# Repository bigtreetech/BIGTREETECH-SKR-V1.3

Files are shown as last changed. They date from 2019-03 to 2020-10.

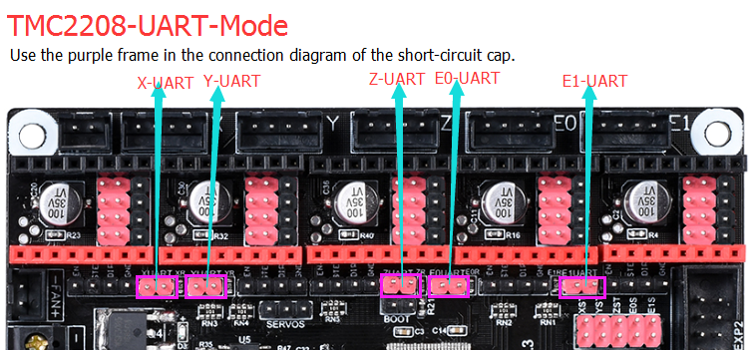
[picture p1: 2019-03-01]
BTT SKR V1.3/Wiring diagram/SKR V1.3-TMC2208-UART-Mode.png

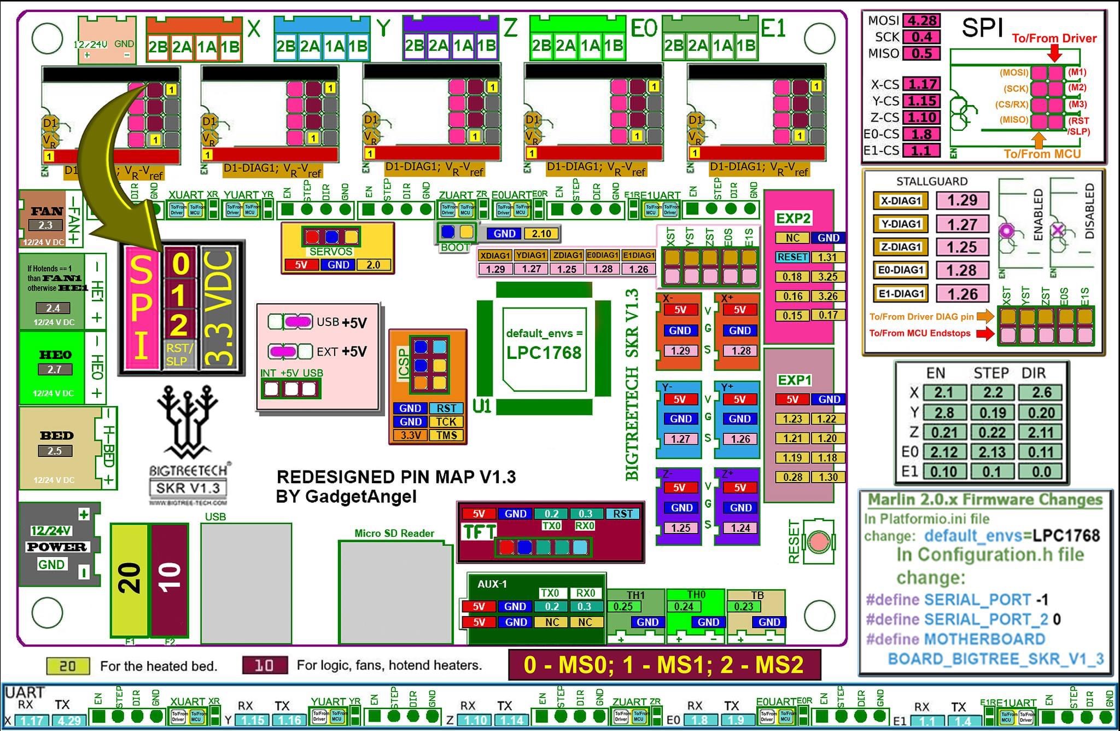
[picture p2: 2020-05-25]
BTT SKR V1.3/hardware/SKR-V1.3-pinout.jpg

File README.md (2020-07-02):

# BIGTREETECH-SKR-V1.3
32bit board with LPC1768, support marlin2.0 and smoothieware, support lcd2004/12864, On-board TMC2130 SPI interface and TMC2208 UART interface no additional wiring is 

BIGTREETECH SKR V1.3 YouTube Video：[here](https://www.youtube.com/watch?v=oaXfXkPYHpw&t=8s)
 
# BIGTREETECH-SKR-V1.4
This [article](https://3dwork.io/en/complete-guide-skr-v1-4-and-tmc2209) explains how to configure all different TMC2209 dirvers from different procuders in SKR V1.4 & V1.4 Turbo

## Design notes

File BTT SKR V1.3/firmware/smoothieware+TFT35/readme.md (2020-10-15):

If you are using smootheware firmware, please disable the LEDs event in the configuration file,  as shown below
> leds_disable                        true

> play_led_disable                    true



Because there is no led on SKR V1.3, and the IO used by the LED on smoothieboard is of other use in SKR V1.3. If the LED is not disabled, other functions may be abnormal

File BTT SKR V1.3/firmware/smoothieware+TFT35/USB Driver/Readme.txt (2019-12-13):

USB Driver Installation tutorial £º
                                   http://smoothieware.org/windows-drivers

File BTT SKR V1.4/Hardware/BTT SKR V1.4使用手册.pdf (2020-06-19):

### 深圳市必趣科技有限公司 BIG TREE TECH

# BIGTREETECH SKR V1.4

# 主板使用说明书

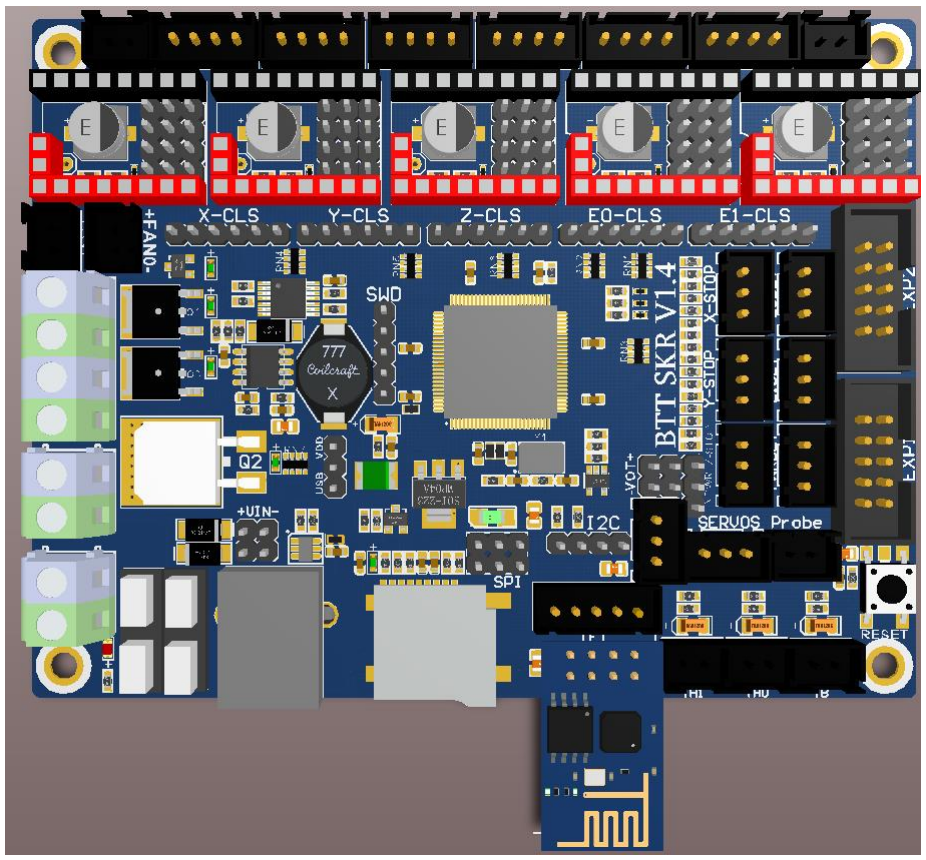
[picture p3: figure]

### BIG TREE TECH

# 一、SKR 主板简介

BIGTREETECH SKR V1.4 主板是深圳必趣科技有限公司 3D 打印

### 团队针对V1.3版本存在的不足进行优化升级的32位3D打印机主板，

### 特别适合中小型打印机使用。

## 1. SKR 主板特点：

1）采用 32 位主频 100MHz 的 ARM 级 Cortex-M3 系列 LPC1768 主控芯片， 性能大幅提升；
2）搭载高度模块化开源固件 Marlin2.0，方便用户 DIY 及二次开发； 3）采用专用电源芯片 M6130，支持 12-24V 电源输入；
4）支持 2.4、2.8、3.5 寸彩色触摸屏，支持 LCD2004 屏、LCD12864 屏； 5）通过 SD 卡升级配置固件，操作简单方便高效；
6）板载 TMC 驱动的 SPI 工作模式和 UART 工作模式，且板载 DIAG 功能引 脚，方便客户使用，省去复杂的接线过程，只需通过简单的拔插跳线帽即可使用； 7）支持断电续打、断料检测、打完关机等功能；
8）采用高性能 MOSFET 管，散热效果更好；
9）采用可拔插的保险丝，是更换过程更加简易；
10）预留 BLTouch 接口 SERVOS 和 Probe，方便使用 BL Touch；
11）支持 RGB 灯条；
12）使用电源选择设计，让 USB 电源与开关电源分开，有效避免由于短路 导致电脑 USB 口被烧毁的情况发生；
13）特殊功能接口使用颜色显眼的排针，大大减少接线的错误率。 14）预留 I2C、SPI、WIFI 接口，方便客户 DIY； 15）预留闭环驱动接口，省去外插转接模块的烦恼；
16）双 Z 轴接口，省去外接驱动拓展模块的烦恼；
17）热敏电阻接口使用胆电容加压敏电阻进行保护，增强接口的抵抗能力； 18）更多的风扇接口：1 路数控风扇，3 路常开风扇；
19）可插外接 DC5V 电源模块，给 TFT 屏、BLtouch、Neopixel 供电。

## 2. SKR 主板参数：

外观尺寸：110*85mm
安装尺寸：102*76mm
微处理器：ARM Cortex-M3 CPU
输入电压：DC12V-DC24V 5A-15A
逻辑电压：DC 3.3V
WIFI 模块：ESP-01S
电机驱动器：支持 TMC5161、TMC5160、TMC2209、TMC2225、TMC2208、 TMC2130、ST820、LV8729、DRV8825、A4988 等，可单独外接电机驱动 驱动工作模式支持：SPI、UART、STEP/DIR

### BIG TREE TECH

电机驱动接口：X、Y、Z、E0、E1，五路（各路都有一个闭环驱动接口）， 最高可达 256 细分
温度传感器接口：TH0、TH1、TB，3 路 100K NTC（热电阻） 显示屏：2.4、2.8、3.5 寸 TFT（支持双模式屏）、LCD2004、LCD12864 PC 通信接口：方形 USB，方便插拔，通信波特率 115200 拓展接口功能支持：断料检测，断电续打，打完关机，自动调平，BL Touch 支持文件格式：G-code
支持机器结构：XYZ、delta、kossel、Ultimaker、corexy 推荐软件：Cura、Simplify3D、pronterface、Repetier-host、Makerware

# 二、SKR 主板通电

SKR 主板上电之后，左下角的 D5 红灯会亮起，表示供电正常；板子中部的 5V SEL 是电源选择端；
1）当使用 USB 给主板供电时：

2）当使用 12V-24V 供电时：

# 三、SKR 主板与电脑通信

SKR 主板通过【USB】接口与电脑通信，需要电脑先安装驱动程序后，再将 主板插入电脑，方可识别端口进行数据传输。不安装驱动程序就容易出现电脑无 法识别 USB 端口的现象，
使用 Marlin2.0 固件，则是参照教程进行安装：

教程：https://www.dropbox.com/s/ppjfflhf3j5yzh2/MarlinV2.0%20SKRV1.1%20instruction.docx?dl=0驱动：https://www.dropbox.com/s/a0k5idjmf4fn82f/lpc176x_usb_driver.inf?dl=0

# 四、SKR 主板接口说明

1. SKR 主板尺寸图

### BIG TREE TECH

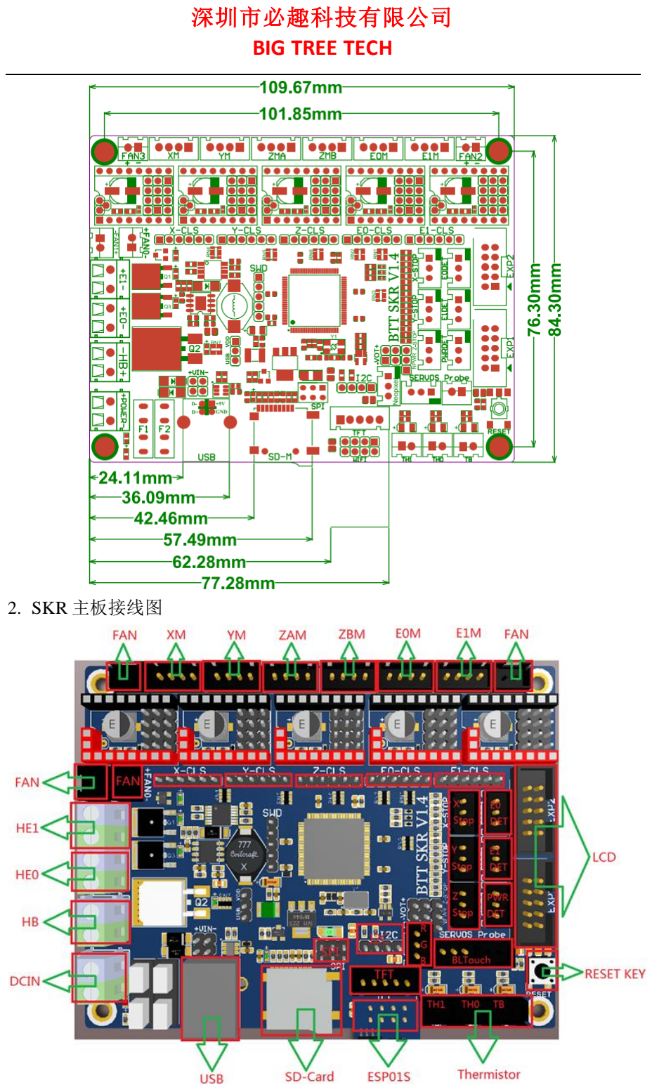
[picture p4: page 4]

2. SKR 主板接线图

### BIG TREE TECH

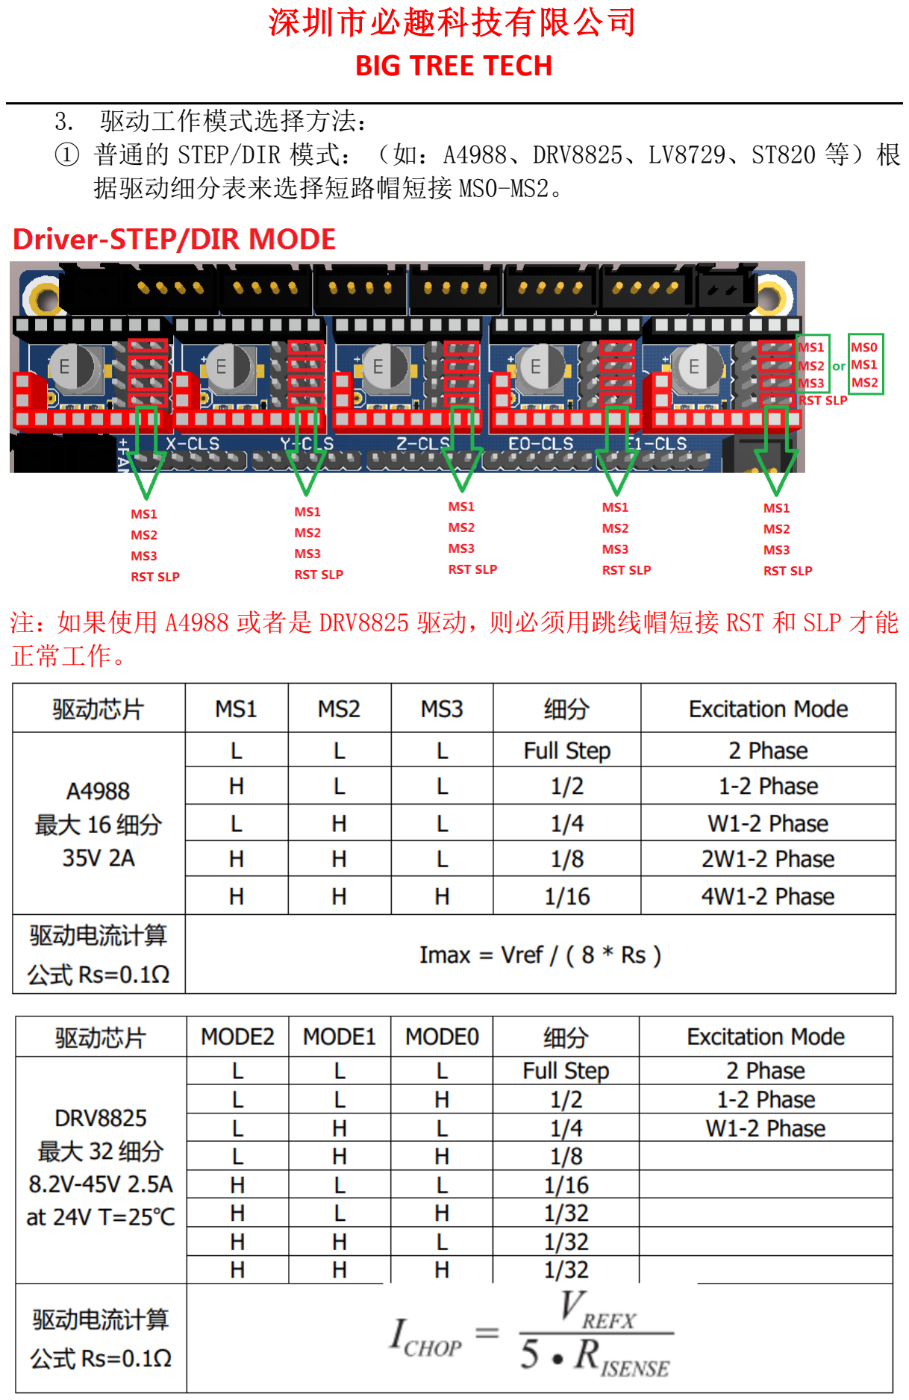
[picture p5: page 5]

3. 驱动工作模式选择方法：
① 普通的 STEP/DIR 模式：（如：A4988、DRV8825、LV8729、ST820 等）根 据驱动细分表来选择短路帽短接 MS0-MS2。

注：如果使用 A4988 或者是 DRV8825 驱动，则必须用跳线帽短接 RST 和 SLP 才能 正常工作。

### BIG TREE TECH

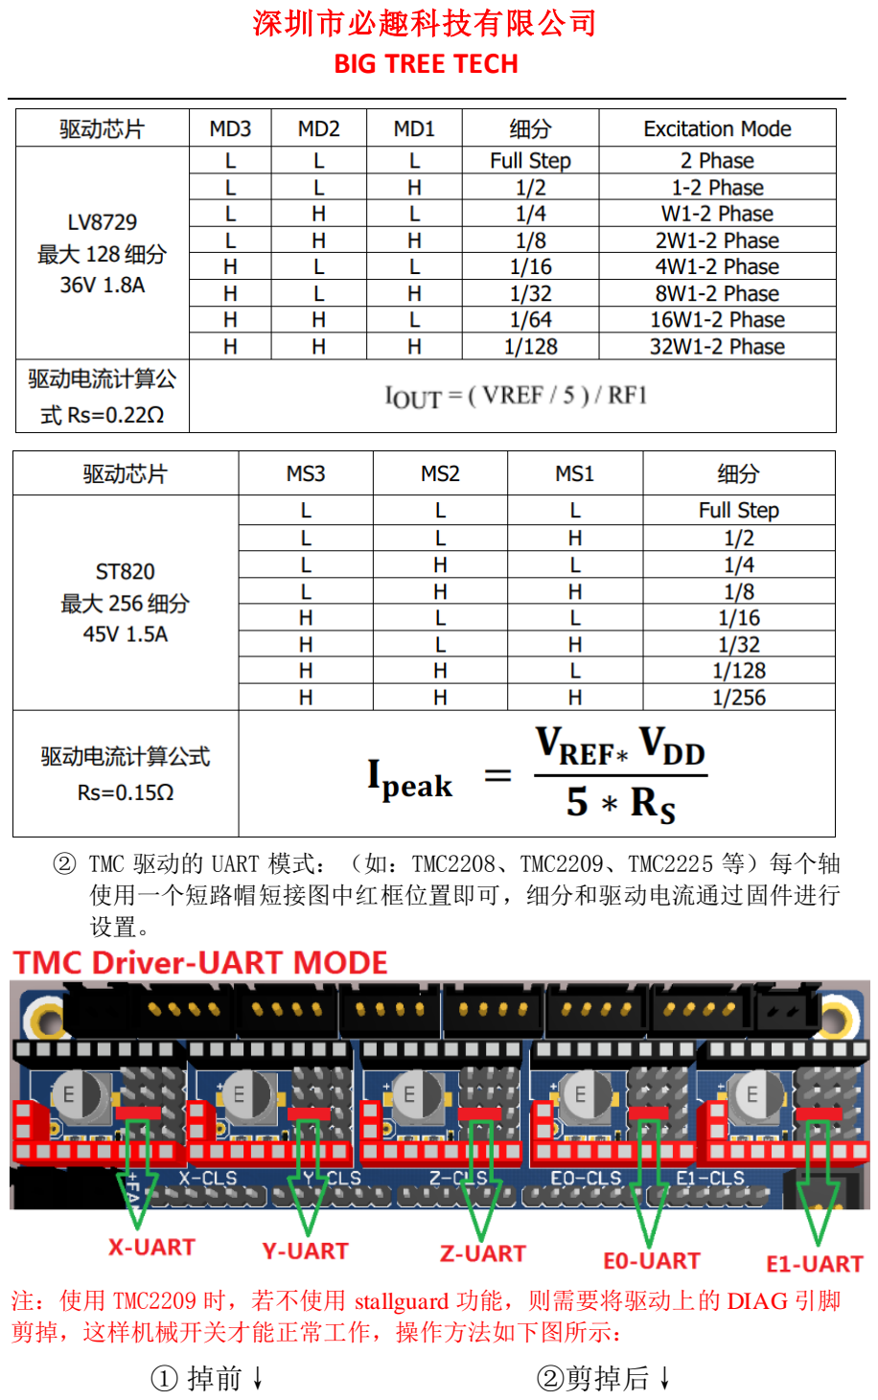
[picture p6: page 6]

② TMC 驱动的 UART 模式：（如：TMC2208、TMC2209、TMC2225 等）每个轴 使用一个短路帽短接图中红框位置即可，细分和驱动电流通过固件进行 设置。

注：使用 TMC2209 时，若不使用 stallguard 功能，则需要将驱动上的 DIAG 引脚 剪掉，这样机械开关才能正常工作，操作方法如下图所示：
① 掉前↓ | ②剪掉后↓

### BIG TREE TECH

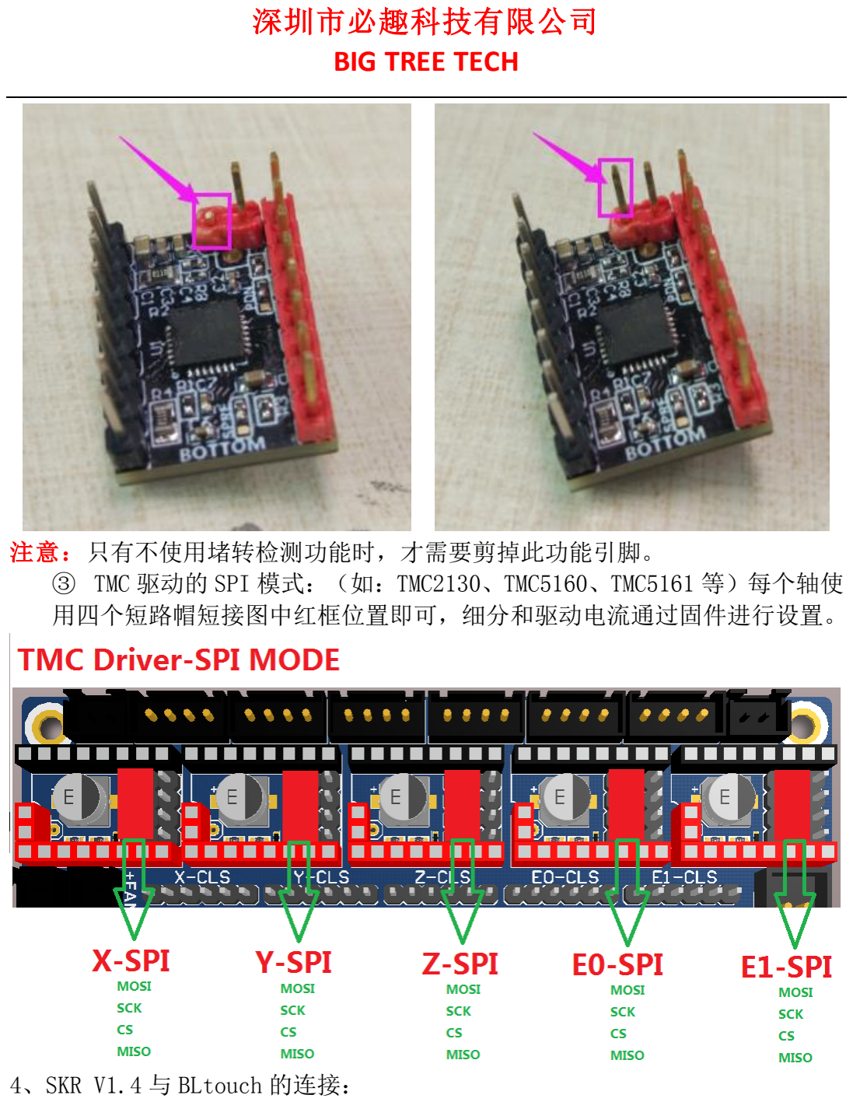
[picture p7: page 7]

注意：只有不使用堵转检测功能时，才需要剪掉此功能引脚。
③ TMC 驱动的 SPI 模式：（如：TMC2130、TMC5160、TMC5161 等）每个轴使 用四个短路帽短接图中红框位置即可，细分和驱动电流通过固件进行设置。

4、SKR V1.4 与 BLtouch 的连接：

### BIG TREE TECH

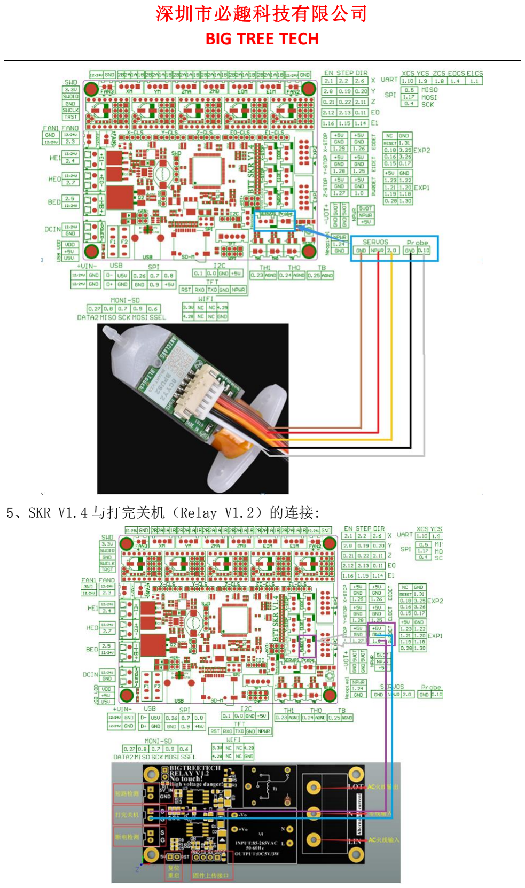
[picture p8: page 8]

5、SKR V1.4 与打完关机（Relay V1.2）的连接:

### BIG TREE TECH

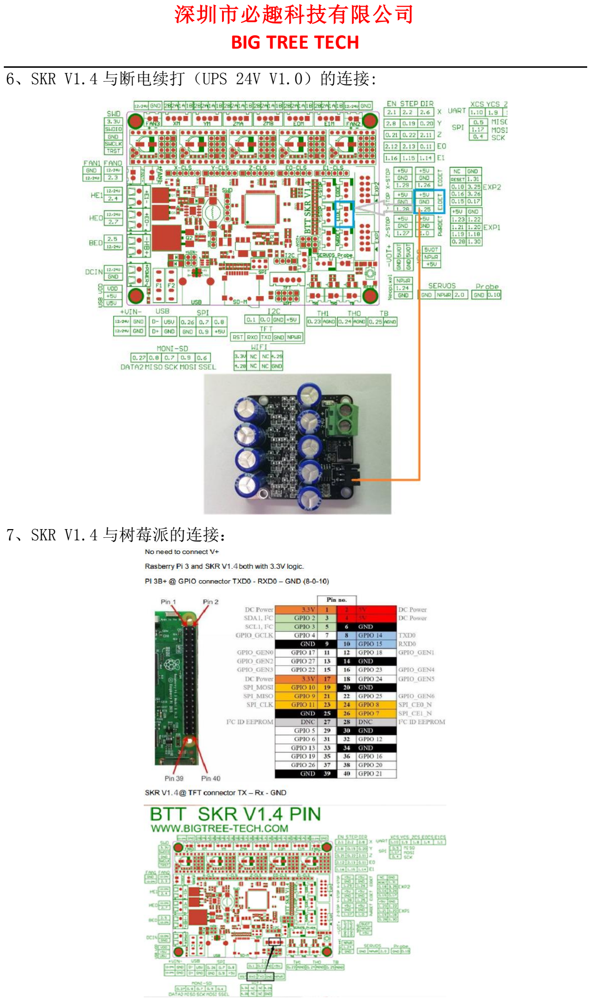
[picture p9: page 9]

6、SKR V1.4 与断电续打（UPS 24V V1.0）的连接:

7、SKR V1.4 与树莓派的连接：

### BIG TREE TECH

8、SKR V1.4 与闭环驱动的连接：

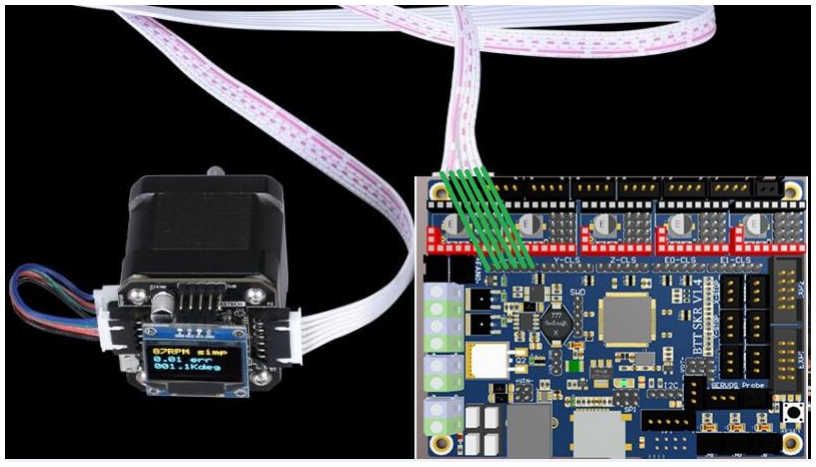
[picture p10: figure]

# 五、SKR 主板固件说明

出厂的主板里会装有测试使用的固件（I3 机型），可以直接使用，也可根据己 需自行更改。
1.SKR 主板固件获取方式
问客服或者技术人员获取；
我司开原网址进行下载：https://github.com/bigtreetech 2.Marlin2.0 固件更新方法
下载好我司开源的 Marlin2.0 固件后，使用 Visual Studio Code 打开工程进行 编译，然后找到 firmware.bin 文件，复制到 SD 卡中，然后复位主板即可。详 细步骤请参照教程：

https://www.dropbox.com/s/ppjfflhf3j5yzh2/MarlinV2.0%20SKRV1.1%20instruction.docx?dl=0

## 六、注意事项：

### 1.主板 5V SEL 必须连接 VDD 和+5V 两个引脚，方可进行打印（即

### 必须有 12V-24V 电源给主板供电才能进行打印）；

### 2.主板所接热床功率必须小于等于 144W（即热床电阻值大于 1

### Ω），要是用大功率热床时，必须外接热床功率扩展板；

### 3.SD 卡中的固件文件名字不可更改（包括大小写）；

### 4.接线过程和插驱动过程必须是在断电前提下进行，在检查线路

### BIG TREE TECH

### 正确连接及驱动正确插入后方可上电，防止接错线导致主板和驱动被

### 烧毁，造成不必要的损失；

### 5.若要更换配置文件，请将出厂的配置文件备份，以记录各部分

### 芯片引脚标号，然后对新的配置文件进行更改！

### 若您使用中还遇到别的问题，欢迎您联系我们，我们定会细心为

### 您解答；若您对我们的产品有什么好的意见或建议，也欢迎您回

### 馈给我们，我们也会仔细斟酌您的意见或建议，感谢您选择

BIGTREETECH 制品，谢谢！

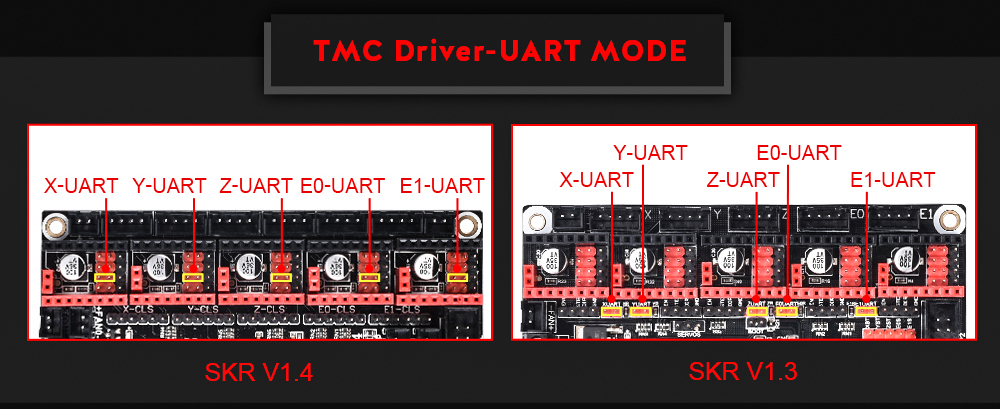
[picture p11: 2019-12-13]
BTT SKR V1.4/Hardware/UART.jpg

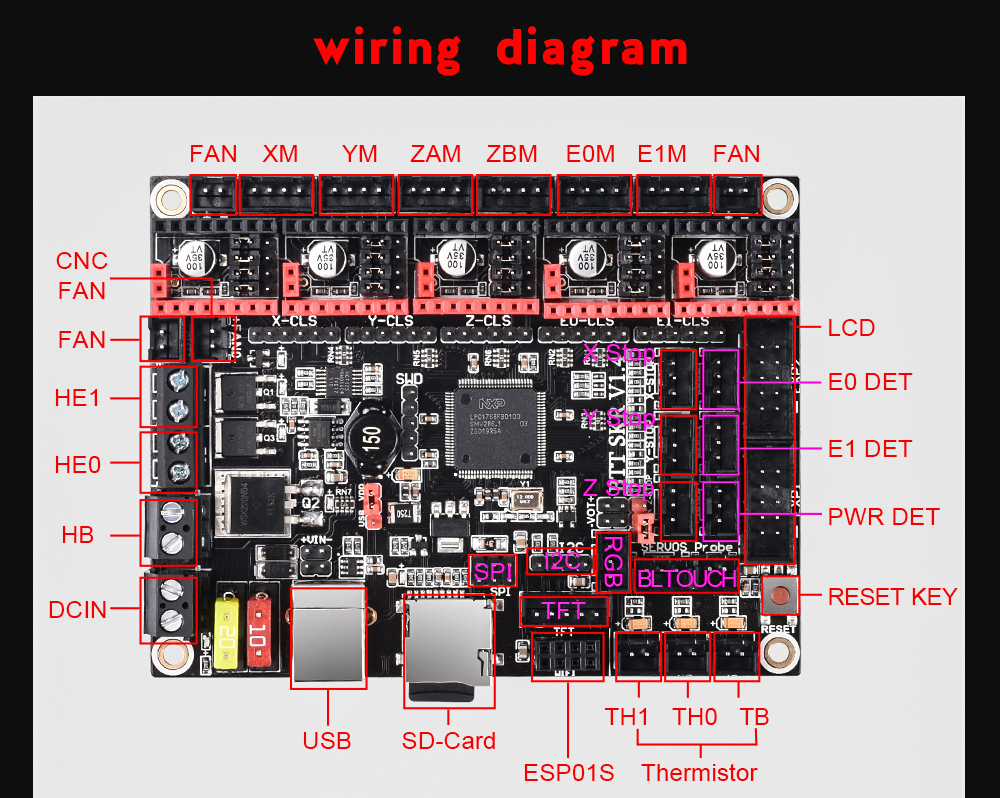
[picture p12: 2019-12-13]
BTT SKR V1.4/Hardware/connect.jpg

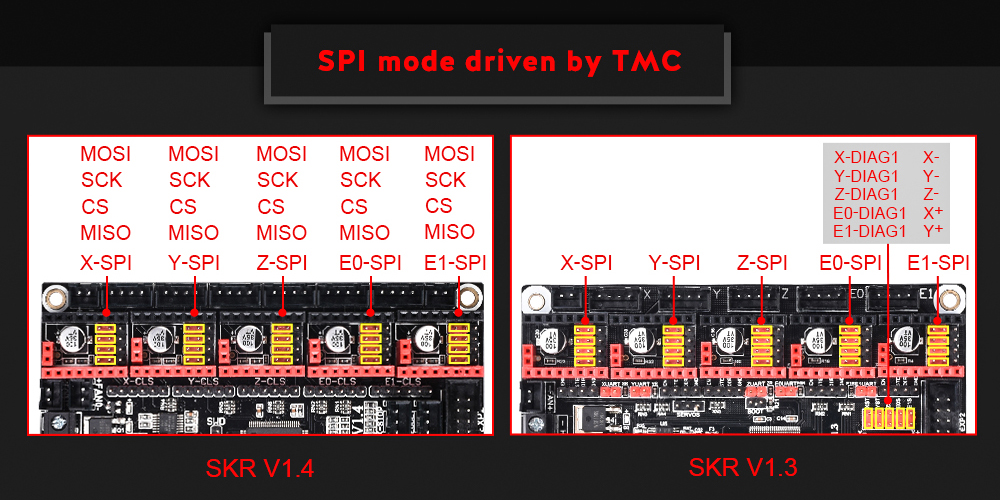
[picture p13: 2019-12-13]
BTT SKR V1.4/Hardware/SPI.jpg

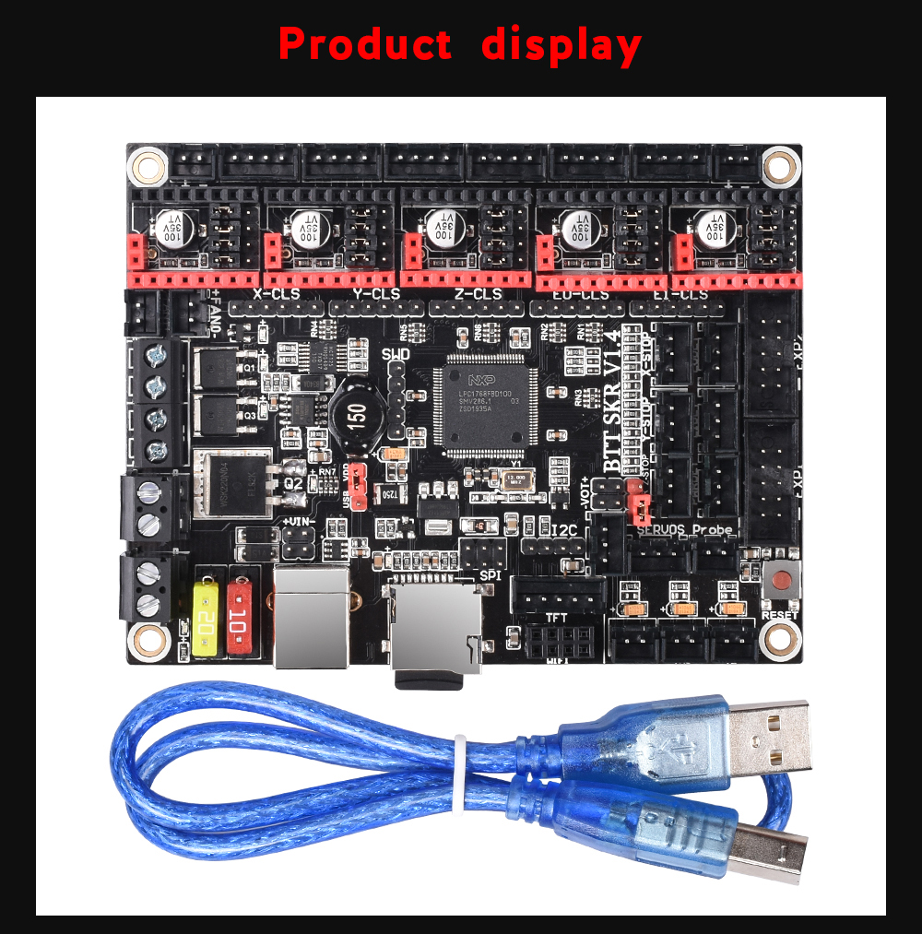
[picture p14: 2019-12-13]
BTT SKR V1.4/Hardware/top.jpg

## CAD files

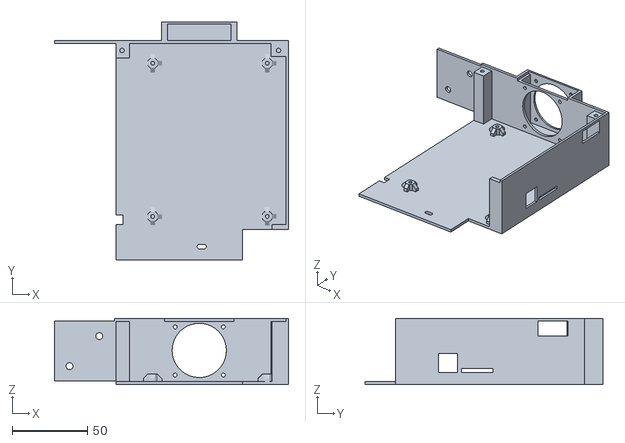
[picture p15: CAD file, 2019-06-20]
BTT SKR V1.3/BigtreeTech SKR 1.3 Case model/Ender 3 case for BigTreeTech SKR board - Bottom Case 40 x 40 x 10 - No fan guard.stl
155.5 x 158.4 x 44.0

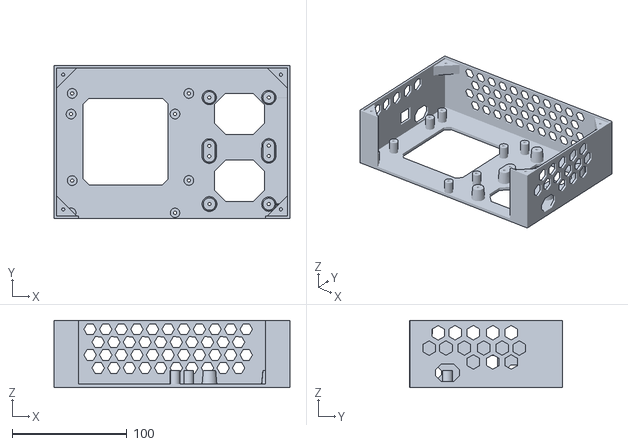
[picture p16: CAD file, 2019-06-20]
BTT SKR V1.3/BigtreeTech SKR 1.3 Case model/Anet A6 - SKR 1.3 motherboard case.stl
206.0 x 133.5 x 58.8

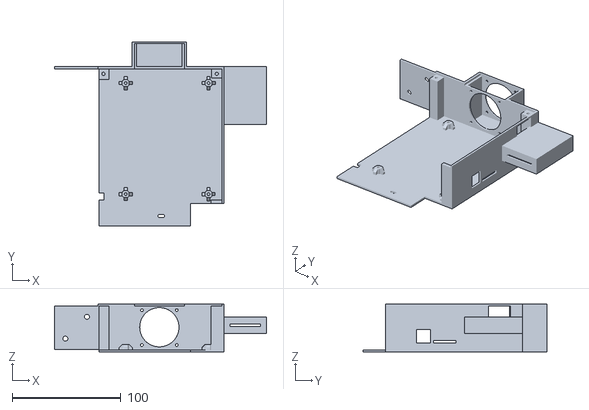
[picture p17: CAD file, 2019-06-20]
BTT SKR V1.3/BigtreeTech SKR 1.3 Case model/Ender 3 case for BigTreeTech SKR board with card slot - Bottom Case - 40 x 40 x 20 No guard.stl
194.5 x 168.4 x 44.0

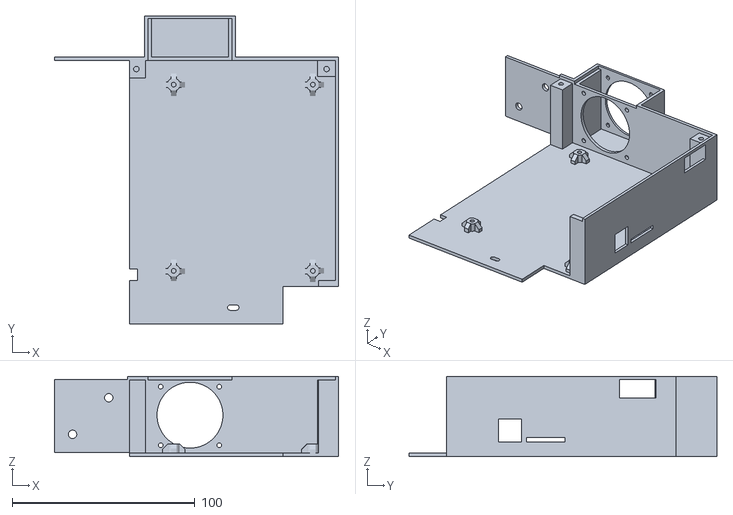
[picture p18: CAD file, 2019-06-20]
BTT SKR V1.3/BigtreeTech SKR 1.3 Case model/Ender 3 case for BigTreeTech SKR board - Bottom Case - 40 x 40 x 20 - No fan guard offset.stl
155.5 x 168.4 x 44.0

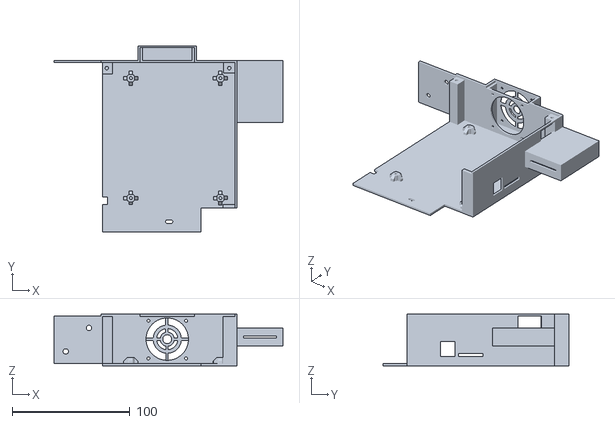
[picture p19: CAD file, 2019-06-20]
BTT SKR V1.3/BigtreeTech SKR 1.3 Case model/Ender 3 case for BigTreeTech SKR board with card slot - Bottom Case - 40 x 40 x 10.stl
194.5 x 158.4 x 44.0

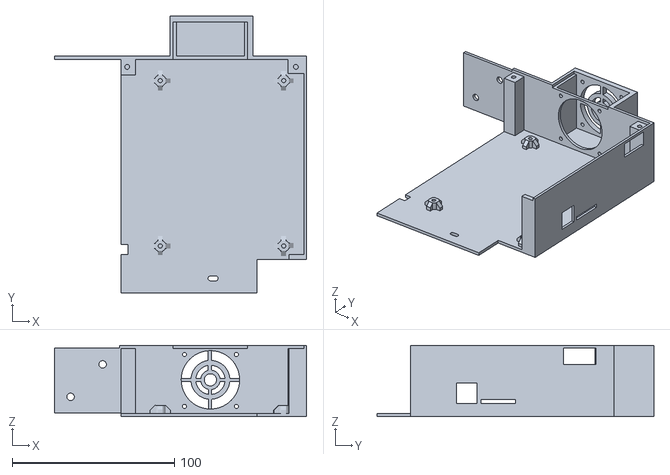
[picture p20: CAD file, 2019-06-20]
BTT SKR V1.3/BigtreeTech SKR 1.3 Case model/Ender 3 case for BigTreeTech SKR board - Bottom Case - 40 x 40 x 20.stl
155.5 x 170.8 x 44.0

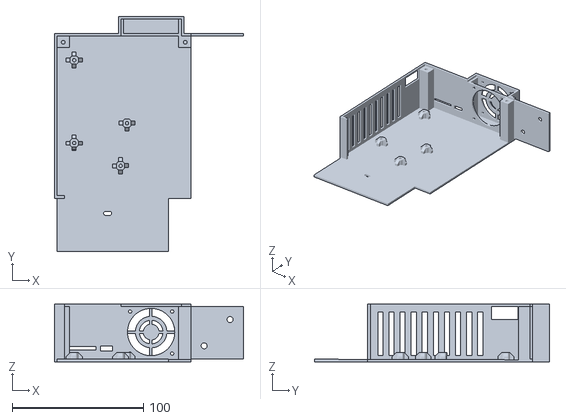
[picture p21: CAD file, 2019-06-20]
BTT SKR V1.3/BigtreeTech SKR 1.3 Case model/Ender 3 Pro - SKR 1_3 board enclosure - Creality board case.stl
144.0 x 179.0 x 44.0

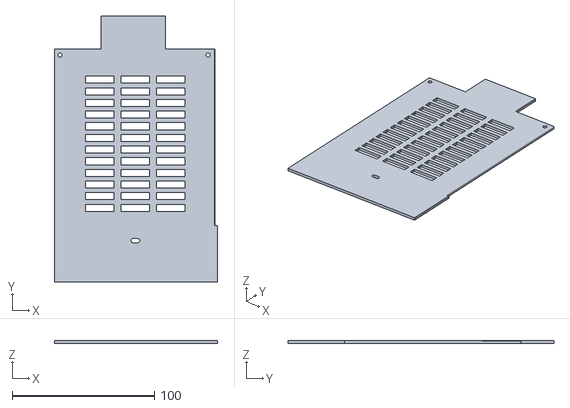
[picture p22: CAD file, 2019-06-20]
BTT SKR V1.3/BigtreeTech SKR 1.3 Case model/Ender 3 case for BigTreeTech SKR board - Top Cover - 40 x 20.stl
114.5 x 186.8 x 2.00

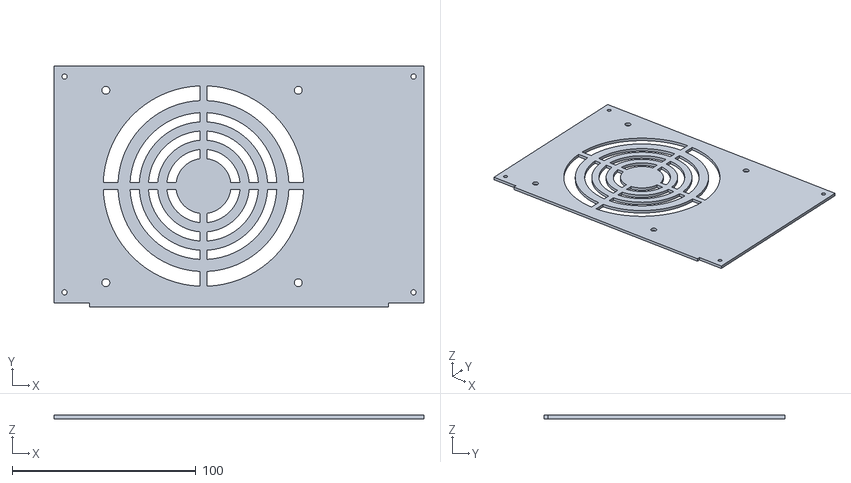
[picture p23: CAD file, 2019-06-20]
BTT SKR V1.3/BigtreeTech SKR 1.3 Case model/Anet A6 - SKR 1.3 motherboard cover 120 x 120 fan.stl
201.5 x 131.2 x 2.00

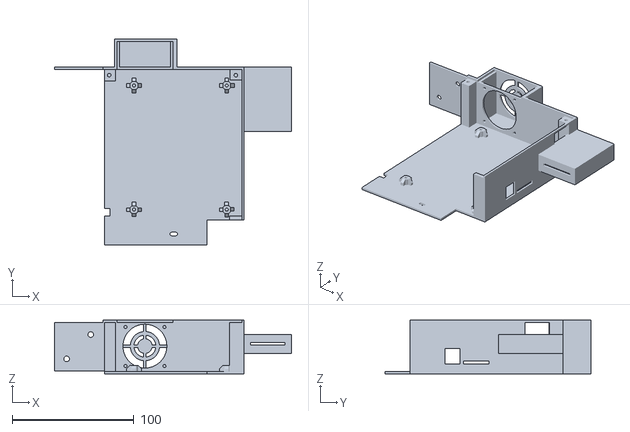
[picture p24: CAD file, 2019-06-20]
BTT SKR V1.3/BigtreeTech SKR 1.3 Case model/Ender 3 case for BigTreeTech SKR board with card slot - Bottom Case - 40 x 20 offset.stl
194.5 x 169.0 x 44.0

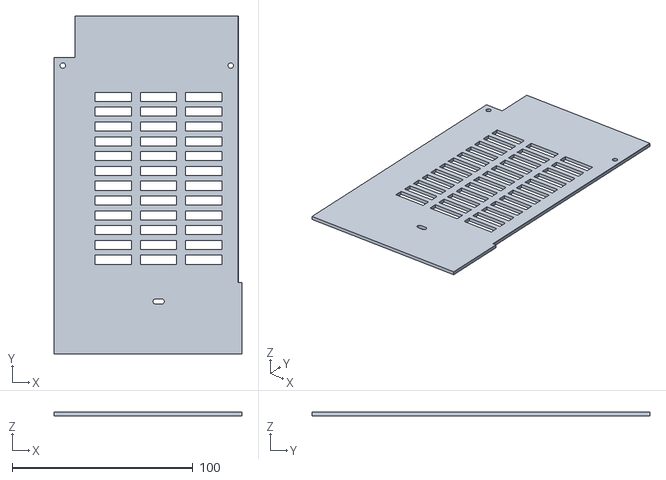
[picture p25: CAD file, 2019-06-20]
BTT SKR V1.3/BigtreeTech SKR 1.3 Case model/Ender 3 Pro - SKR 1_3 board enclosure - Dual fans - 40 x 40 x 20 Cover.stl
103.9 x 186.8 x 2.00

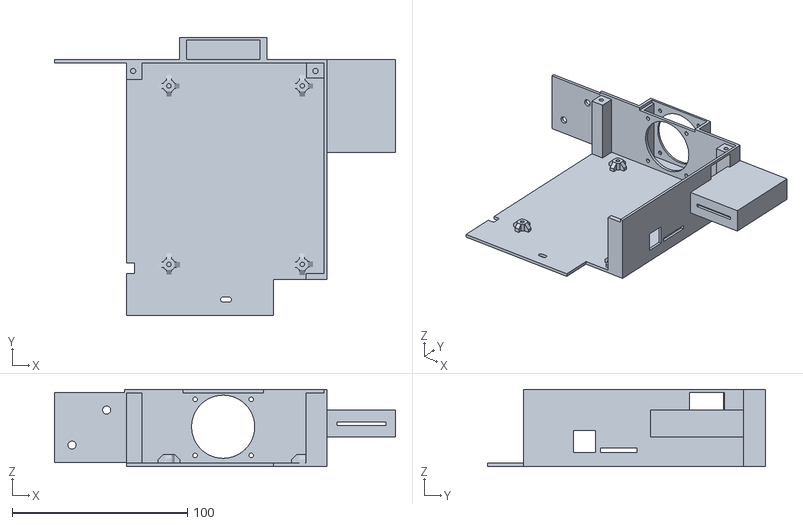
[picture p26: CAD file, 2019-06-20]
BTT SKR V1.3/BigtreeTech SKR 1.3 Case model/Ender 3 case for BigTreeTech SKR board with card slot - Bottom Case - 40 x 40 x 10 No guard.stl
194.5 x 158.4 x 44.0

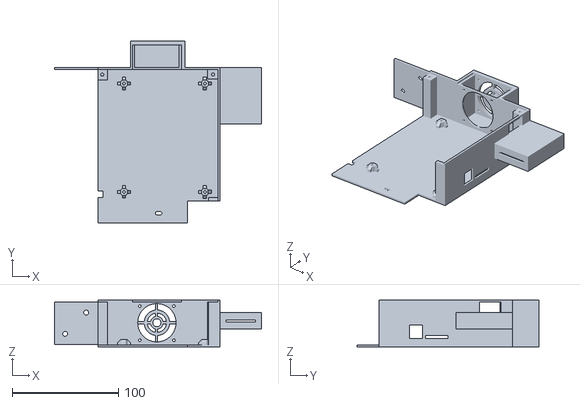
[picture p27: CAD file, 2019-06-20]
BTT SKR V1.3/BigtreeTech SKR 1.3 Case model/Ender 3 case for BigTreeTech SKR board with card slot - Bottom Case - 40 x 20.stl
194.5 x 170.8 x 44.0

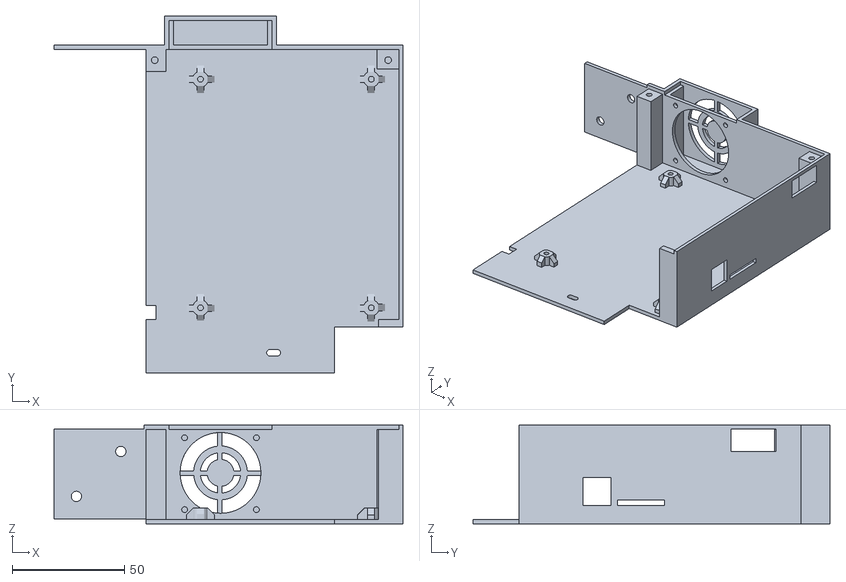
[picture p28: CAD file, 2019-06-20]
BTT SKR V1.3/BigtreeTech SKR 1.3 Case model/Ender 3 case for BigTreeTech SKR board - Bottom Case - 40 x 40 x 10 offset.stl
155.5 x 159.0 x 44.0

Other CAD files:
BTT SKR V1.3/BigtreeTech SKR 1.3 Case model/Ender 3 case for BigTreeTech SKR board with card slot - Bottom Case - 40 x 40 x 20 No guard offset.stl
BTT SKR V1.3/BigtreeTech SKR 1.3 Case model/Ender 3 case for BigTreeTech SKR board - Bottom Case - 40 x 40 x 10 No fan guard offset.stl
BTT SKR V1.3/BigtreeTech SKR 1.3 Case model/Ender 3 case for BigTreeTech SKR board with card slot - Bottom Case - 40 x 40 x 10 offset.stl
BTT SKR V1.3/BigtreeTech SKR 1.3 Case model/BigTreeTech SKR board.stl
BTT SKR V1.3/BigtreeTech SKR 1.3 Case model/Anet A6 - SKR 1.3 motherboard case - 20 x 20 mounting.stl
BTT SKR V1.3/BigtreeTech SKR 1.3 Case model/Anet A6 - SKR 1.3 motherboard cover - 20 x 20 mounting.stl
BTT SKR V1.3/BigtreeTech SKR 1.3 Case model/Anet A6 - SKR 1.3 motherboard cover - 80 x 80 fan.stl
BTT SKR V1.3/BigtreeTech SKR 1.3 Case model/Anet A6 - SKR 1.3 motherboard cover.stl
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

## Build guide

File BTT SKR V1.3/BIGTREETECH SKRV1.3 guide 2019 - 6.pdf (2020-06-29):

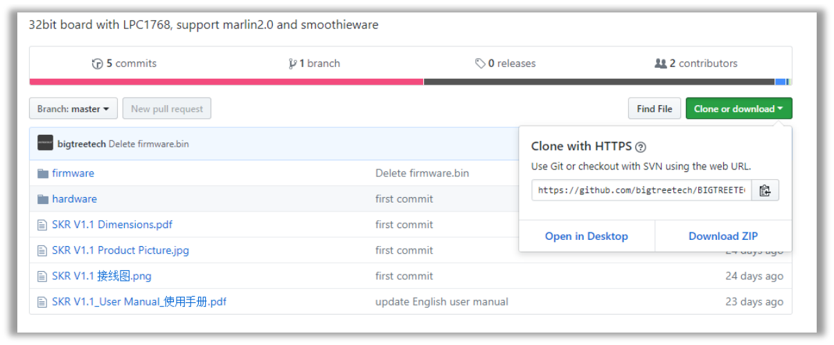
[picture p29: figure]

BIGTREETECH SKR V1.3 guide 2019 – V6 by Jupa Creations Page 1

BIGTREETECH/BIQU SKR V1.3 instruction guide by Jupa Creations

All official information like schematics and hardware about this 32 bits 3D printer mainboard can be found on the BIGTREETECH official GITHUB site. (https://github.com/bigtreetech/BIGTREETECH-SKR-V1.3)

This instruction guide is to show you how to install Marlin 2.0 firmware to the SKR V1.3 board in general and some extra stuff. It does not take in account machine and other hardware specific settings!

This document is based for Windows OS systems.

You can use VSCode or Atom.IO + Platform IO to compile Marlin2.0 to BIGTREETECH SKR V1.3

Intended for use with a REPRAP_DISCOUNT_FULL_GRAPHIC_SMART_CONTROLLER 128x64 LCD display by standard with two 10 pin wire ribbon cables.

Download the Marlin2.0 firmware from Marlin 2.0 github firmware version (https://github.com/MarlinFirmware/Marlin/tree/bugfix-2.0.x) and click.

Click “Download ZIP”

In general the BIGTREETECH firmware version on their Github page is outdated, so do not use it. In any case download Marlin 2.0 github firmware version (https://github.com/MarlinFirmware/Marlin/tree/bugfix-2.0.x) and modify it to your needs.

When the download is complete, unzip the file to a known place.

In this example we use VScode

Download the VScode from https://code.visualstudio.com/Download. Choose the version which is compliant with your PC operating system.

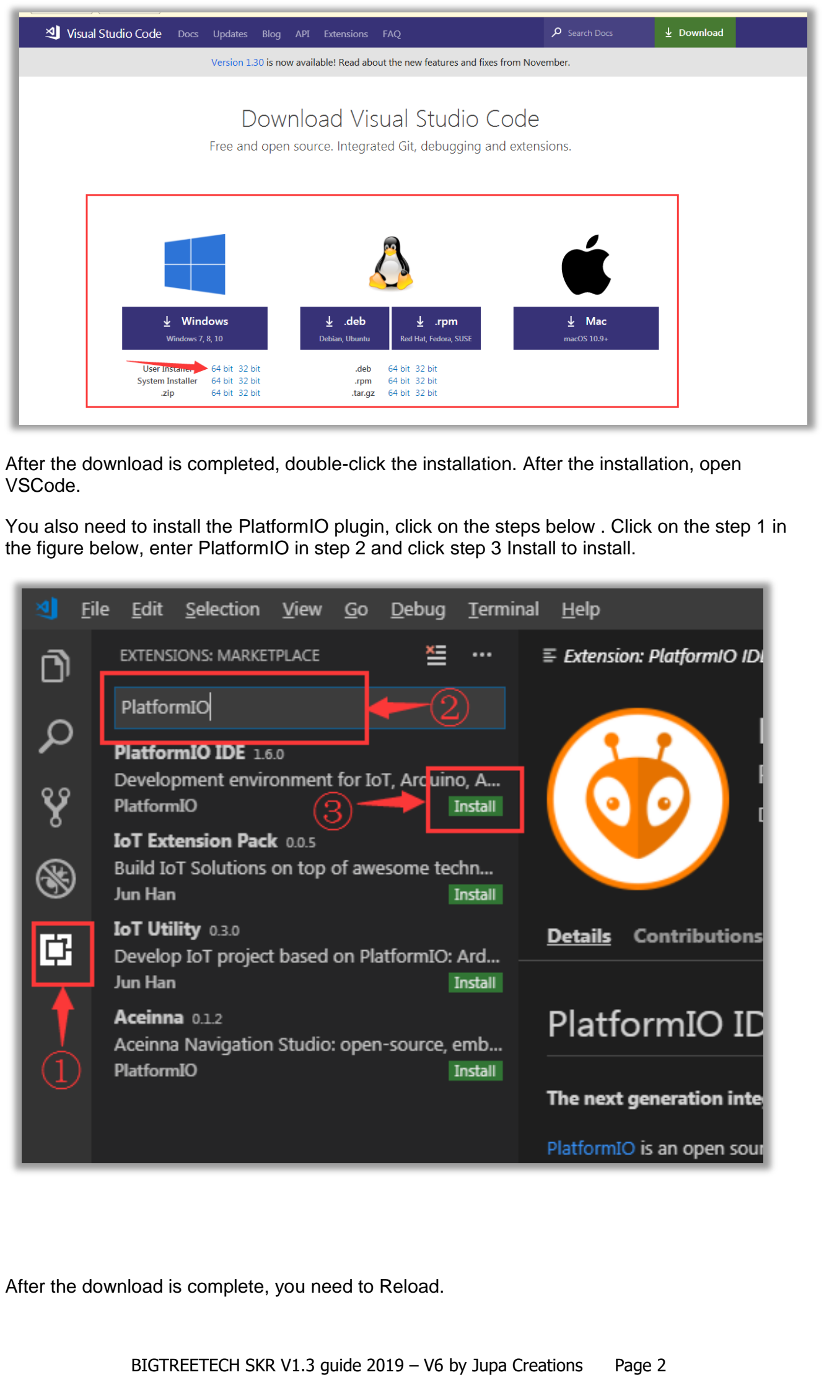
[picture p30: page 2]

BIGTREETECH SKR V1.3 guide 2019 – V6 by Jupa Creations Page 2

After the download is completed, double-click the installation. After the installation, open VSCode.

You also need to install the PlatformIO plugin, click on the steps below . Click on the step 1 in the figure below, enter PlatformIO in step 2 and click step 3 Install to install.

After the download is complete, you need to Reload.

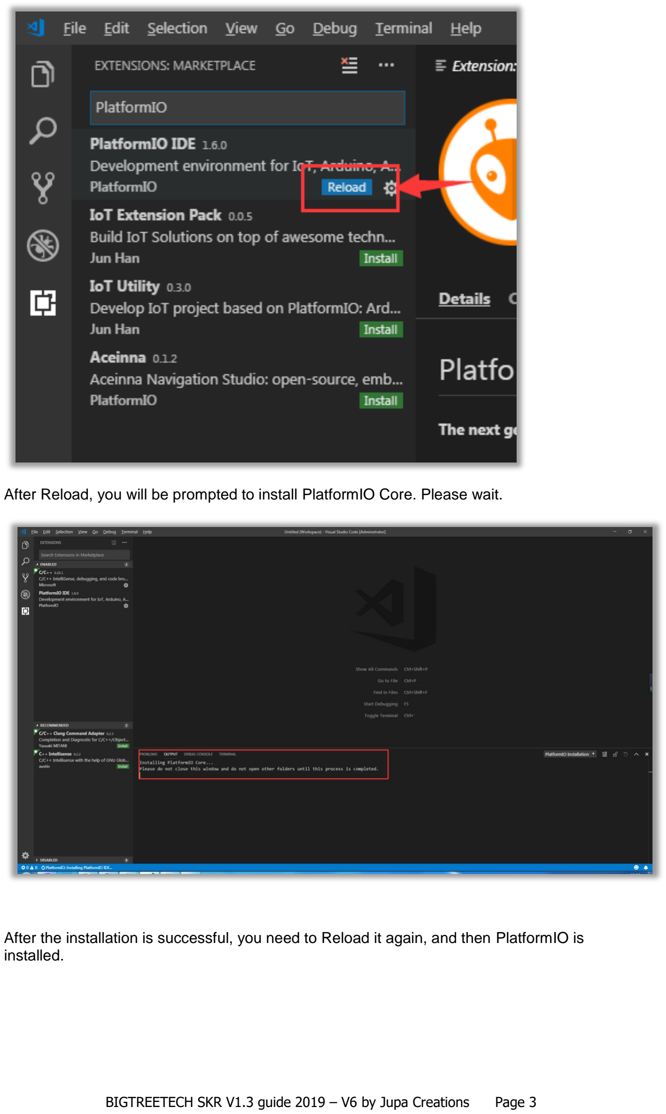
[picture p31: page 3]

BIGTREETECH SKR V1.3 guide 2019 – V6 by Jupa Creations Page 3

After Reload, you will be prompted to install PlatformIO Core. Please wait.

After the installation is successful, you need to Reload it again, and then PlatformIO is installed.

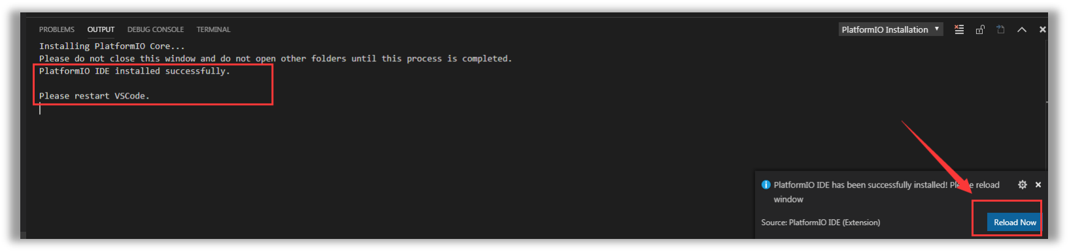
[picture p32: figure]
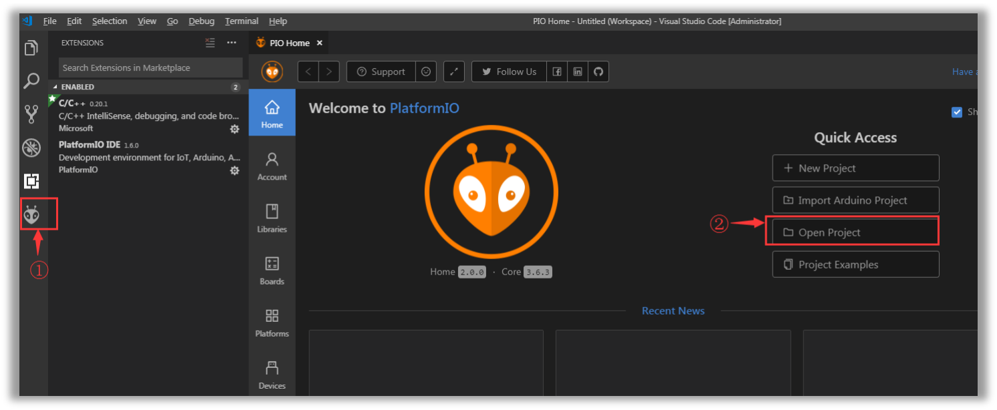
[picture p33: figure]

BIGTREETECH SKR V1.3 guide 2019 – V6 by Jupa Creations Page 4

In the lower left corner of VSCode, you can see the icon (1), which is PlatformIO plug-in. Click
(2) Open Project to Open the Project.

Find the marlin2.0 source directory where you extracted in the very first step, and click Open.

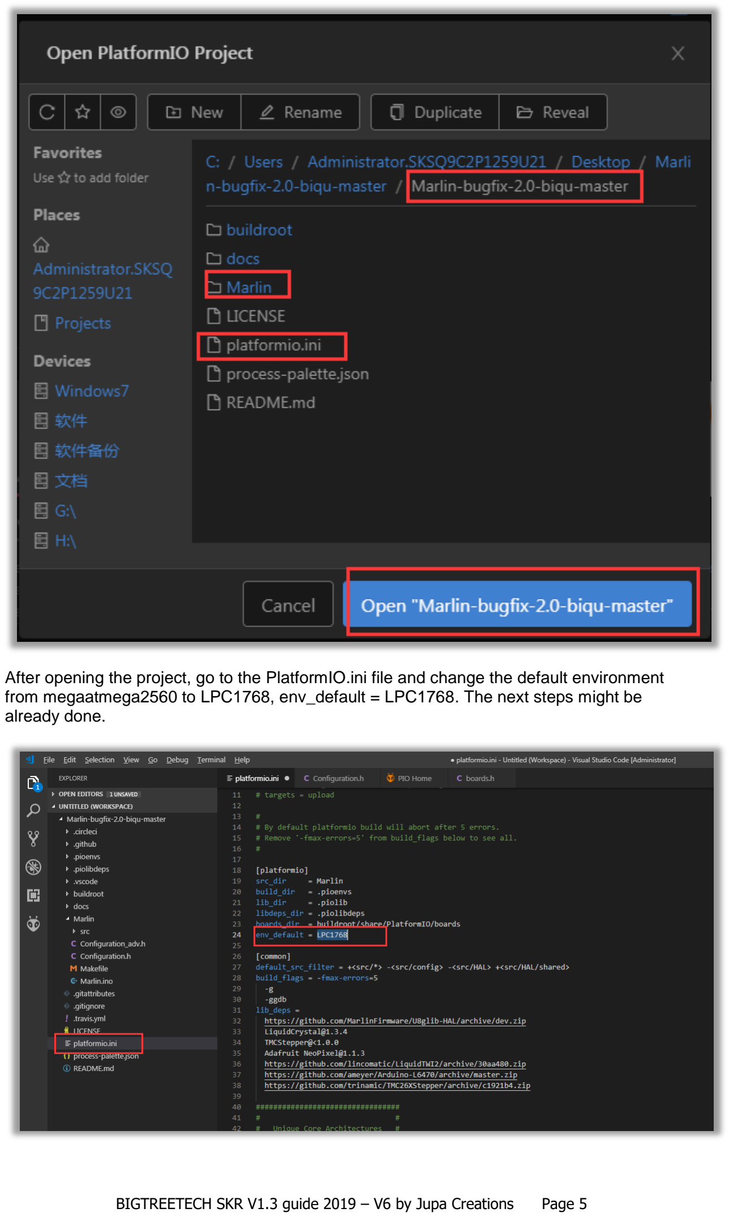
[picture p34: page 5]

BIGTREETECH SKR V1.3 guide 2019 – V6 by Jupa Creations Page 5

After opening the project, go to the PlatformIO.ini file and change the default environment from megaatmega2560 to LPC1768, env_default = LPC1768. The next steps might be already done.

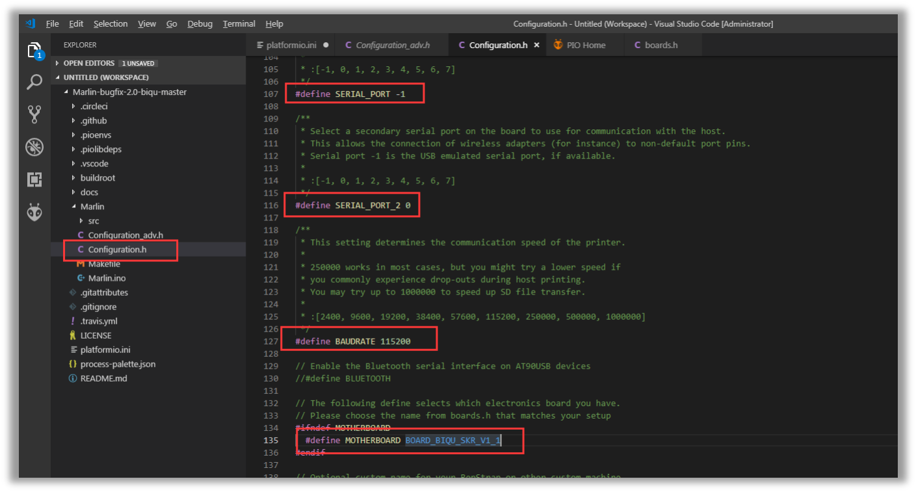
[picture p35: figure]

BIGTREETECH SKR V1.3 guide 2019 – V6 by Jupa Creations Page 6

Then go to the configuration.h file and if not yet done modify it to

#define SERIAL_PORT -1

#define SERIAL_PORT_2 0

#define BAUDRATE 115200 or 250000 depending on your needs.

#define MOTHERBOARD BOARD_BIGTREE_SKR_V1_3

If you like to use a BL-touch (http://marlinfw.org/docs/configuration/probes.html#bed-probes) you have to change some code.

In the same Configuration.h

Modify the following lines:

//#define BLTOUCH and change to
#define BLTOUCH

//#define AUTO_BED_LEVELING_BILINEAR and change to #define AUTO_BED_LEVELING_BILINEAR

// #define Z_SAFE_HOMING and change to
#define Z_SAFE_HOMING

// #define ENCODER_PULSES_PER_STEP 4 and change to #define ENCODER_PULSES_PER_STEP 4

// #define REVERSE_ENCODER_DIRECTION and change to
#define REVERSE_ENCODER_DIRECTION

//#define REPRAP_DISCOUNT_FULL_GRAPHIC_SMART_CONTROLLER and change to #define REPRAP_DISCOUNT_FULL_GRAPHIC_SMART_CONTROLLER

If you like to activate Babystepping (http://marlinfw.org/docs/gcode/M290.html) switch to Configuration_adv.h

//#define BABYSTEPPING and change to
#define BABYSTEPPING

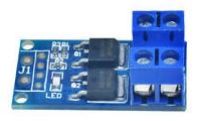
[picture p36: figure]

BIGTREETECH SKR V1.3 guide 2019 – V6 by Jupa Creations Page 7

//#define DOUBLECLICK_FOR_Z_BABYSTEPPING and change to #define DOUBLECLICK_FOR_Z_BABYSTEPPING

//#define BABYSTEP_ZPROBE_OFFSET and change to #define BABYSTEP_ZPROBE_OFFSET

//#define BABYSTEP_ZPROBE_GFX_OVERLAY and change to #define BABYSTEP_ZPROBE_GFX_OVERLAY

#define BABYSTEP_MULTIPLICATOR 1 and change to

#define BABYSTEP_MULTIPLICATOR 20

If your original BL-touch, clone TL-touch or clone BT-touch is dropping the pin during printing switch to Marlin/scr/inc/conditionals_LCD.h and change the following code:

#define BLTOUCH_STOW 100 // was 90

#define BLTOUCH_SELFTEST 130 // was 120

Fan setup

Layer fan

If you like to use a layer fan, connect it to the FAN (http://marlinfw.org/docs/gcode/M106.html) connector.

Heater fan

If you like to make the heater cooling fan controlled with automatic ON/OFF @ 50 degrees Celsius. Connect the fan to the HE1 output and go to configuration_adv.h file.

//#define E0_AUTO_FAN_PIN -1 and change to
#define E0_AUTO_FAN_PIN FAN1_PIN

Driver fan

If you like a board, case or driver fan controlled when drivers are activated go to the configuration_adv.h file

Change to

#define USE_CONTROLLER_FAN

#if ENABLED(USE_CONTROLLER_FAN)

#define CONTROLLER_FAN_PIN P1_26 | // Set a custom pin for the controller fan

#define CONTROLLERFAN_SECS 60 | // Duration in seconds afterrun

#define CONTROLLERFAN_SPEED 255 | // 255 == full speed

#endif

On the Y-max endstop input connect a small mosfet switch with a JST XH2.54 connector on P1-26 and GND.

Sample picture and link (https://www.ebay.nl/itm/15A-400W-MOS-FET-Trigger-Switch-Drive-Module-PWM-Regulator-Control-Panel/233200669989)

BIGTREETECH SKR V1.3 guide 2019 – V6 by Jupa Creations Page 8

After the modification is completed, for VScode press the Ctrl+Shift+B keys or the build icon to start the compiling.
PlatformIO will automatically download the compile component and then compile.

Compiling can take up to 5 minutes, so be patient.

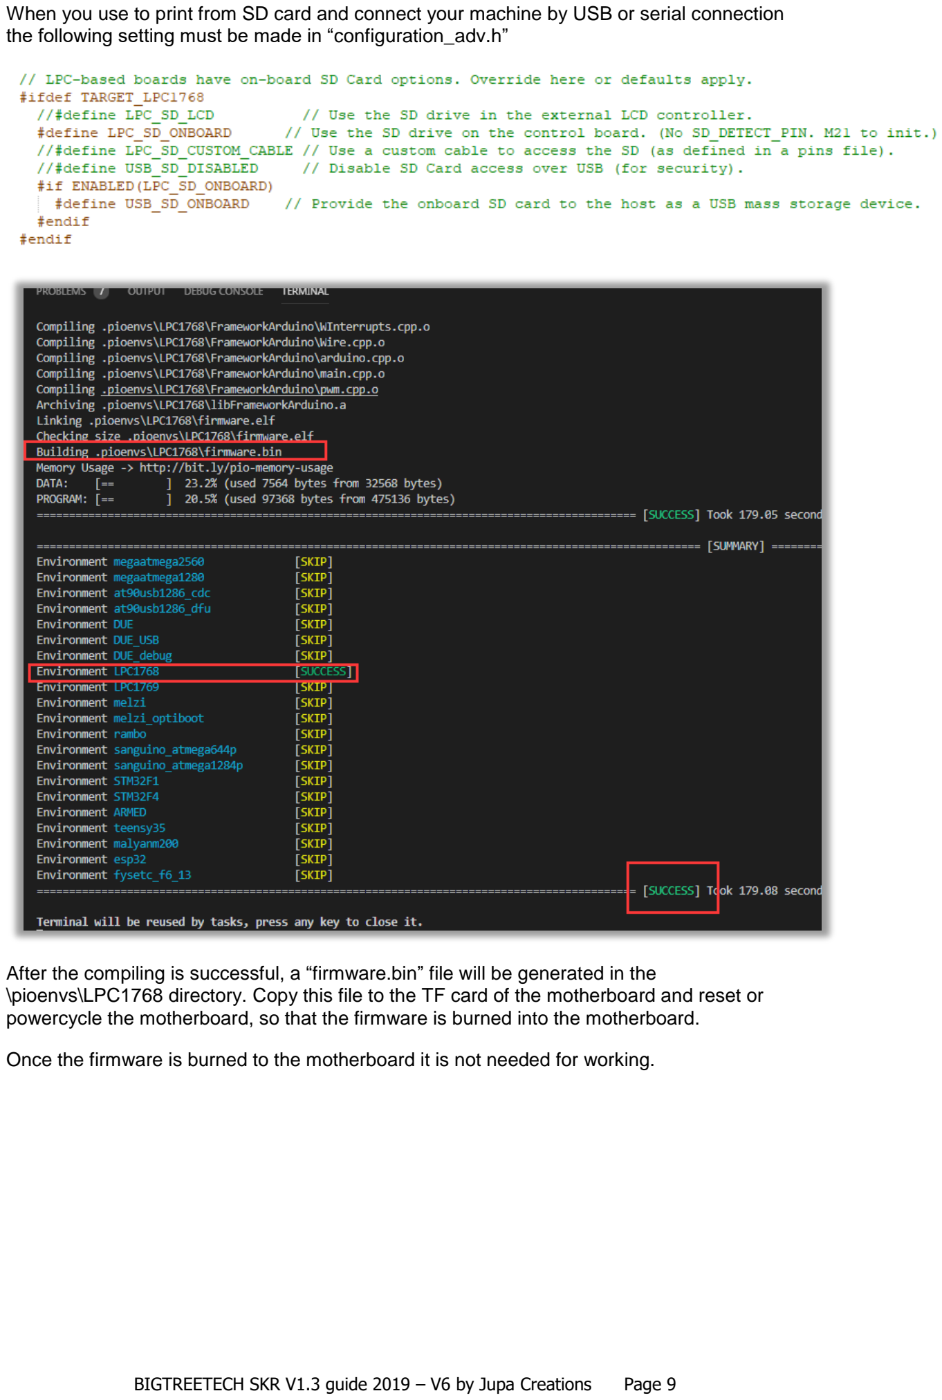
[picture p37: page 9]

BIGTREETECH SKR V1.3 guide 2019 – V6 by Jupa Creations Page 9

When you use to print from SD card and connect your machine by USB or serial connection the following setting must be made in “configuration_adv.h”

After the compiling is successful, a “firmware.bin” file will be generated in the \pioenvs\LPC1768 directory. Copy this file to the TF card of the motherboard and reset or powercycle the motherboard, so that the firmware is burned into the motherboard.

Once the firmware is burned to the motherboard it is not needed for working.

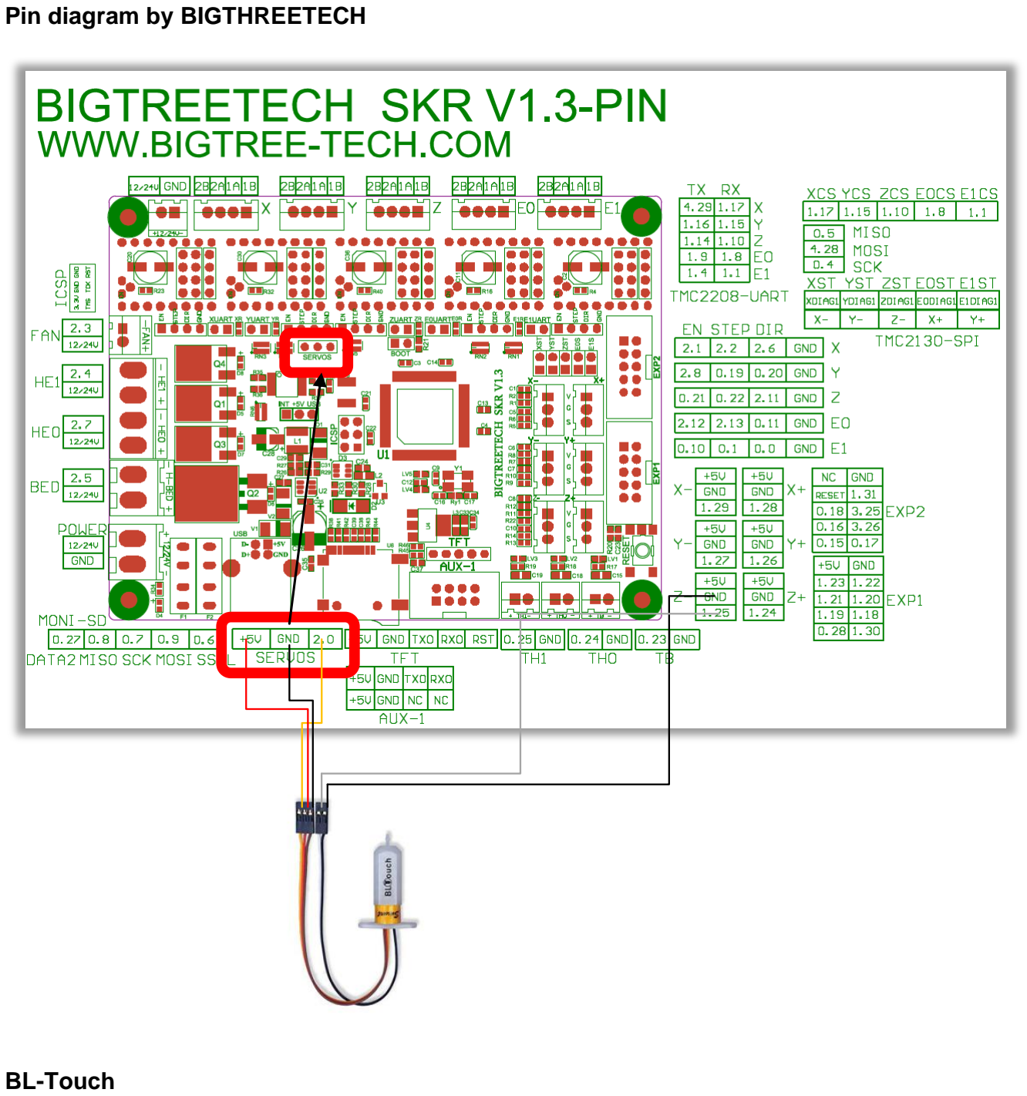
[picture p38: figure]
Pin diagram by BIGTHREETECH; BL-Touch

BIGTREETECH SKR V1.3 guide 2019 – V6 by Jupa Creations Page 10

The SKR V1.3 board has a dedicated Servo port.

Wire connections need to be checked before use!

For connecting the ANTCLABS BL-touch three wire cable to the Servo port.
SKR V1.3 Board servo port = (+)(-)(puls) and BL-touch = (-)(+)(puls)
Positive (+) and Minus (-) need to be swapped in the BL-Touch connector or an intermediate connection cable need to be made. The two wire sensor cable connects to the (Z-) port.

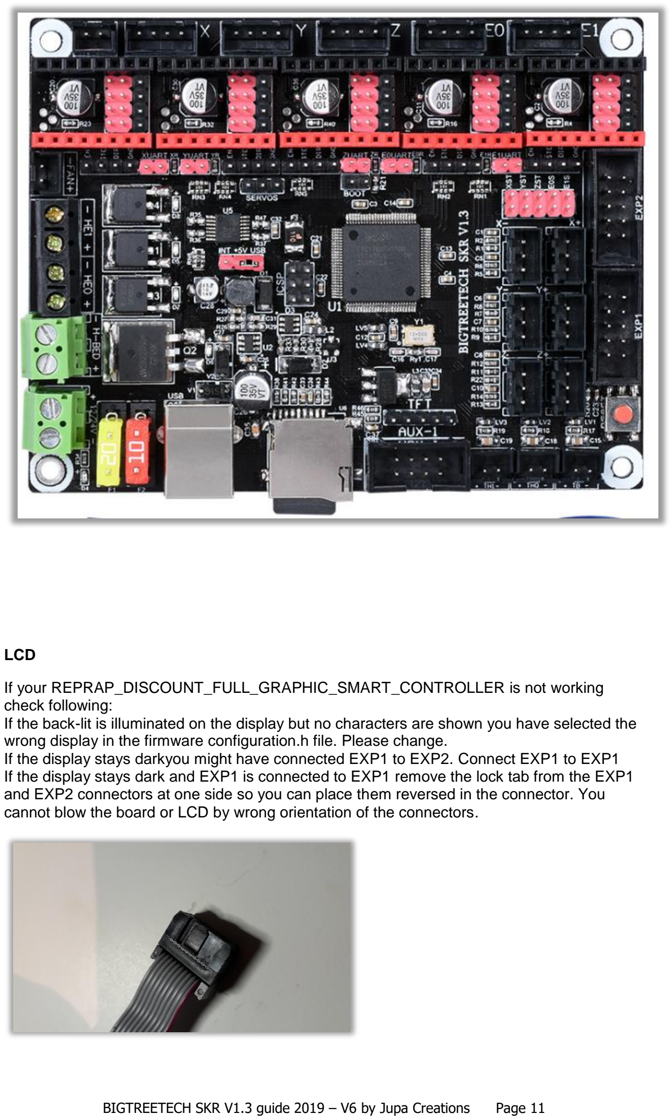
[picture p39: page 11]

BIGTREETECH SKR V1.3 guide 2019 – V6 by Jupa Creations Page 11

LCD

If your REPRAP_DISCOUNT_FULL_GRAPHIC_SMART_CONTROLLER is not working check following:
If the back-lit is illuminated on the display but no characters are shown you have selected the wrong display in the firmware configuration.h file. Please change.
If the display stays darkyou might have connected EXP1 to EXP2. Connect EXP1 to EXP1 If the display stays dark and EXP1 is connected to EXP1 remove the lock tab from the EXP1 and EXP2 connectors at one side so you can place them reversed in the connector. You cannot blow the board or LCD by wrong orientation of the connectors.

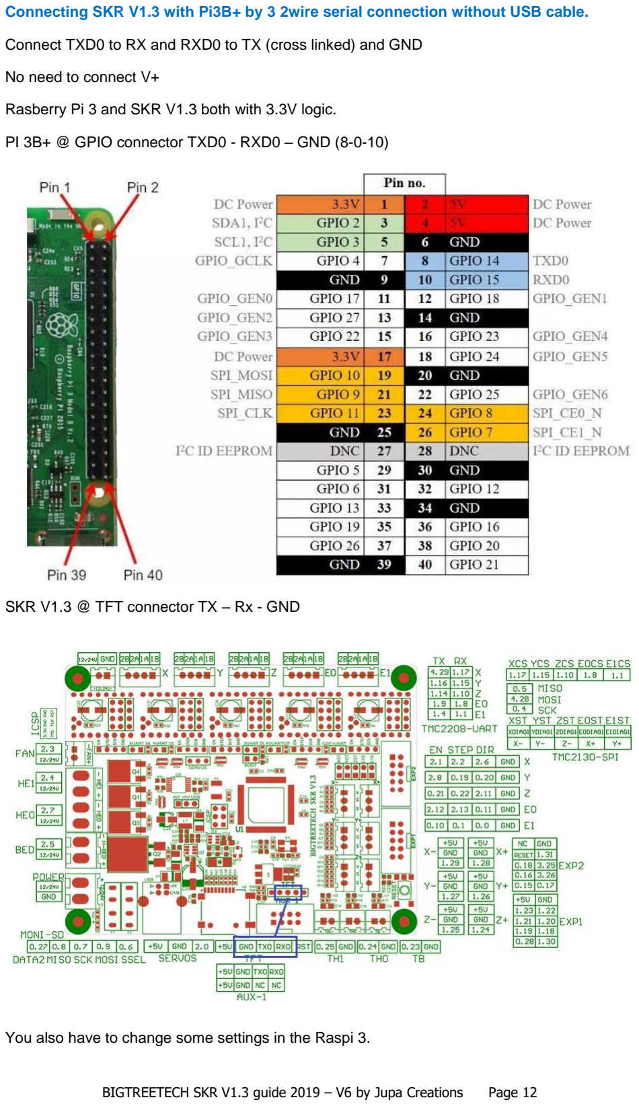
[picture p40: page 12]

BIGTREETECH SKR V1.3 guide 2019 – V6 by Jupa Creations Page 12

Connecting SKR V1.3 with Pi3B+ by 3 2wire serial connection without USB cable.

Connect TXD0 to RX and RXD0 to TX (cross linked) and GND

No need to connect V+

Rasberry Pi 3 and SKR V1.3 both with 3.3V logic.

PI 3B+ @ GPIO connector TXD0 - RXD0 – GND (8-0-10)

SKR V1.3 @ TFT connector TX – Rx - GND

You also have to change some settings in the Raspi 3.

BIGTREETECH SKR V1.3 guide 2019 – V6 by Jupa Creations Page 13

Swapping ports used by GPIO and Bluetooth

The first thing to change in the serial connection is to swap the ports used by the GPIO pins and the internal Bluetooth chip. We need to add a line in the boot config file on the boot partition.

Log in to the Pi3 with SSH on the IP address used.

Type in sudo nano /boot/config.txt

Move the cursor to the end of the file by cursor and add:

dtoverlay=pi3-miniuart-bt

save the file and exit the editor by control+O and control+X

Disabling the serial console

Moving to another config file, where part of the code must be deleted to disable serial console.

Type in sudo nano /boot/cmdline.txt

Look for following string (text) and delete it

console=serial0,115200

save the file and exit the editor by control+O and control+X

Rebooting RPi

For all changes to take effect, please reboot your Raspberry Pi 3

Type in Sudo reboot

Adding the serial port in Octoprint

Last part of the configuration is in the Octoprint web interface. Open your browser and type either "octoprint.local" or the IP address of the Pi 3. You might be greeted with the welcome wizard, please go through it first.

As soon as you arrive at the home screen, open "Settings" (top right), head to "Serial Connection", then "Additional serial ports" and insert following:

/dev/ttyAMA0

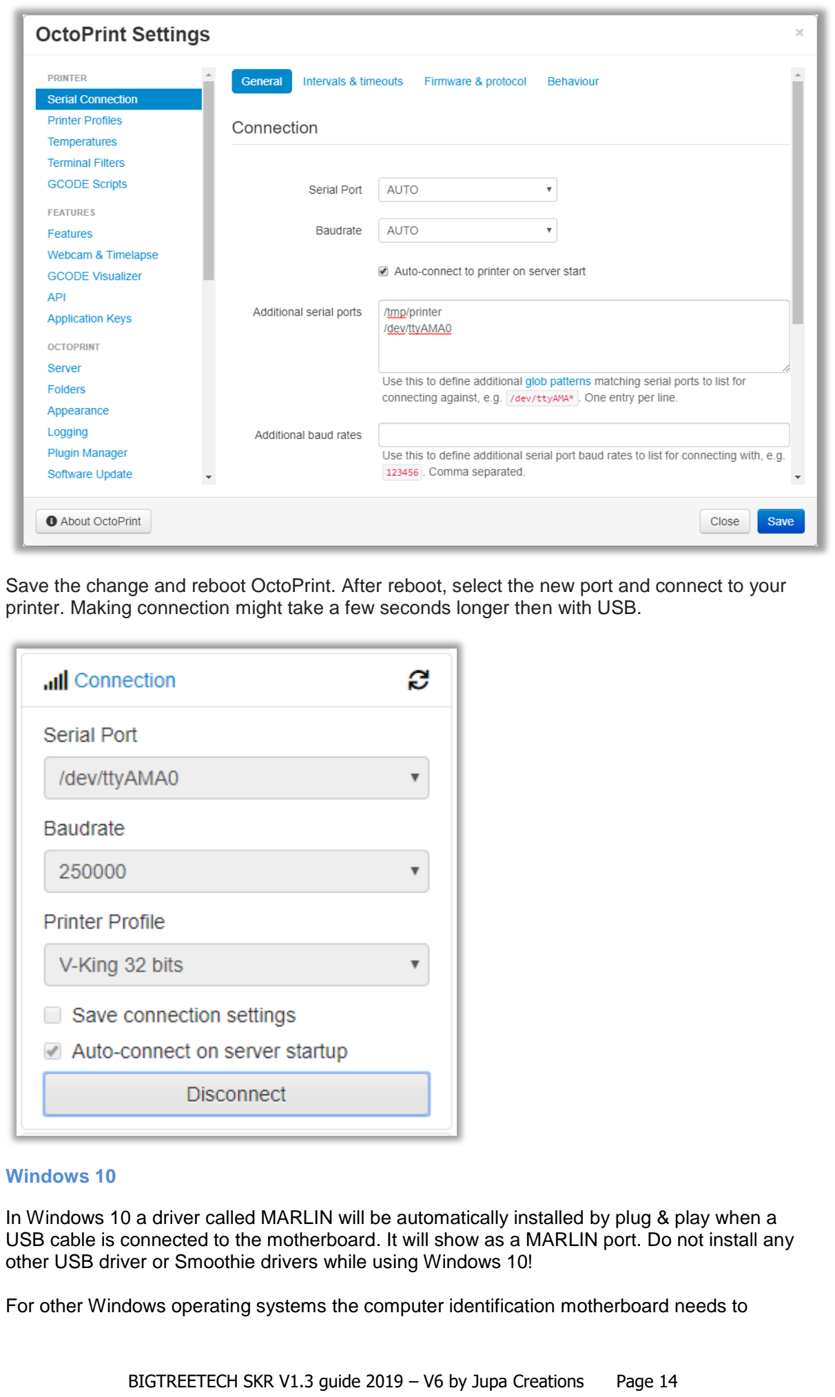
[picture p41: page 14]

BIGTREETECH SKR V1.3 guide 2019 – V6 by Jupa Creations Page 14

Save the change and reboot OctoPrint. After reboot, select the new port and connect to your printer. Making connection might take a few seconds longer then with USB.

Windows 10

In Windows 10 a driver called MARLIN will be automatically installed by plug & play when a USB cable is connected to the motherboard. It will show as a MARLIN port. Do not install any other USB driver or Smoothie drivers while using Windows 10!

For other Windows operating systems the computer identification motherboard needs to

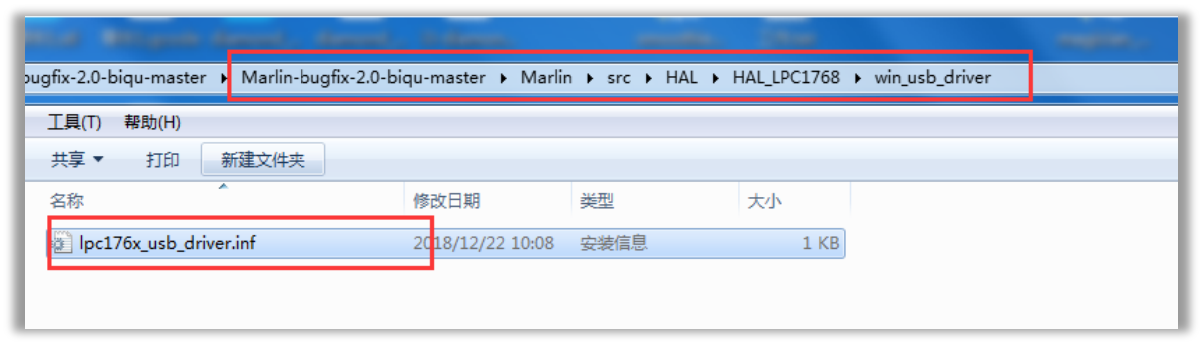
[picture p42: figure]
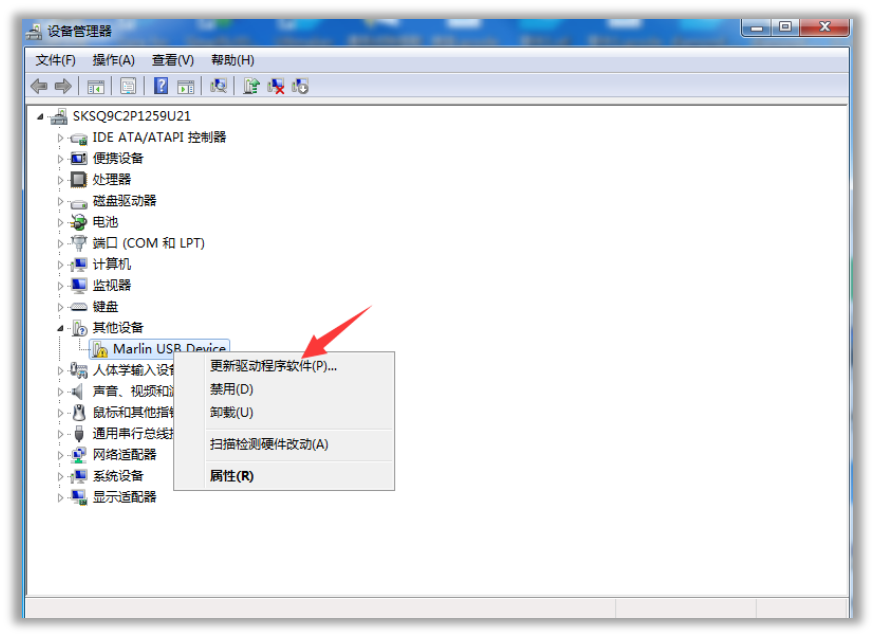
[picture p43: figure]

BIGTREETECH SKR V1.3 guide 2019 – V6 by Jupa Creations Page 15 install USB to serial port driver manually in the directory of the firmware as shown below. Because its path is too long, copy it to an easy to find location like to the desktop.

Open the Device manager, you can see that there is an unrecognized Marlin USB Device, click to update the driver software.

Browse the computer to find the driver software.

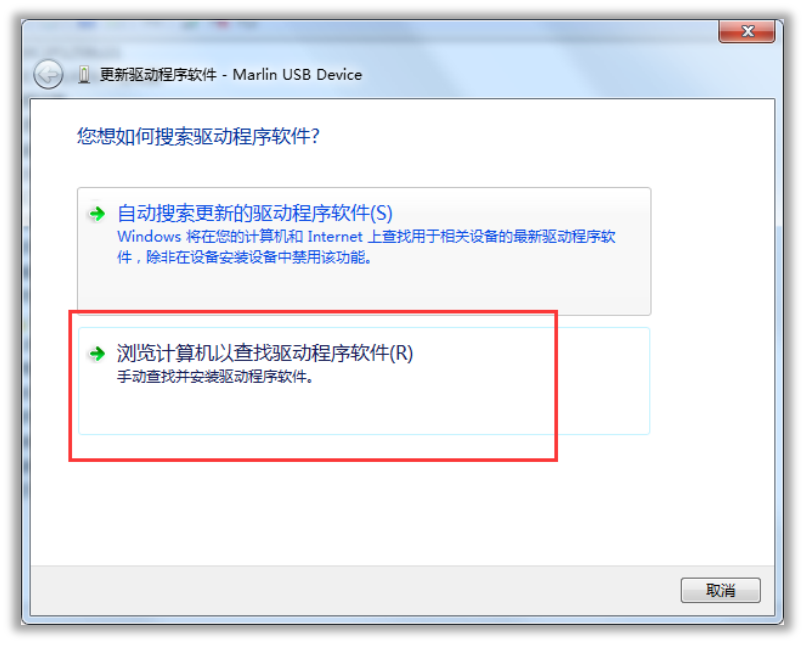
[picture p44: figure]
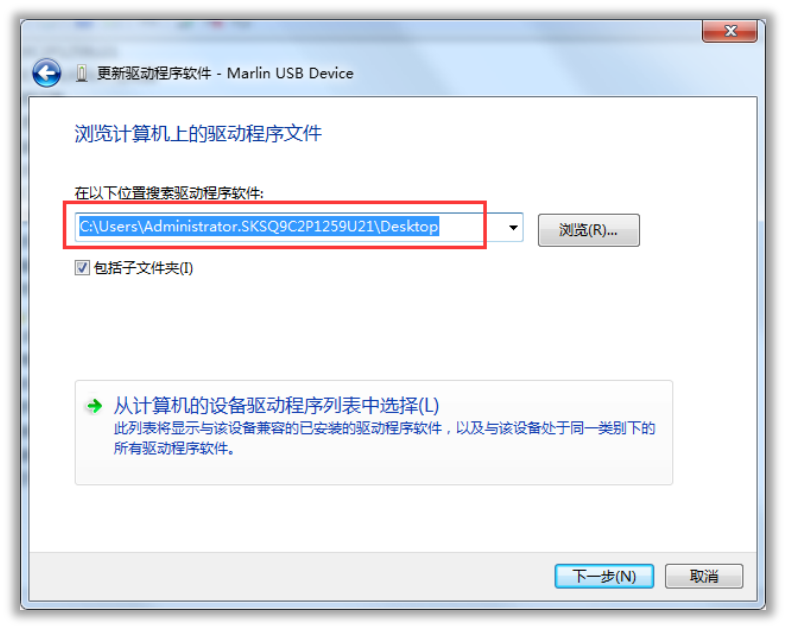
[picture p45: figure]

BIGTREETECH SKR V1.3 guide 2019 – V6 by Jupa Creations Page 16

Select the path as the directory where the lpc176x_usb_driver.inf driver is located. We copied it to the desktop before, so select the desktop location: C:\Users\(Users Name)\Desktop and click Next. Check with the below picture.

If you have firewall alerts, choose to always install this driver software.

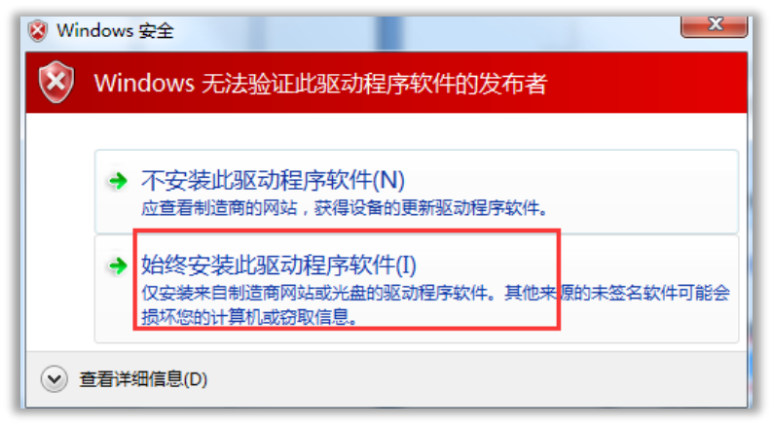
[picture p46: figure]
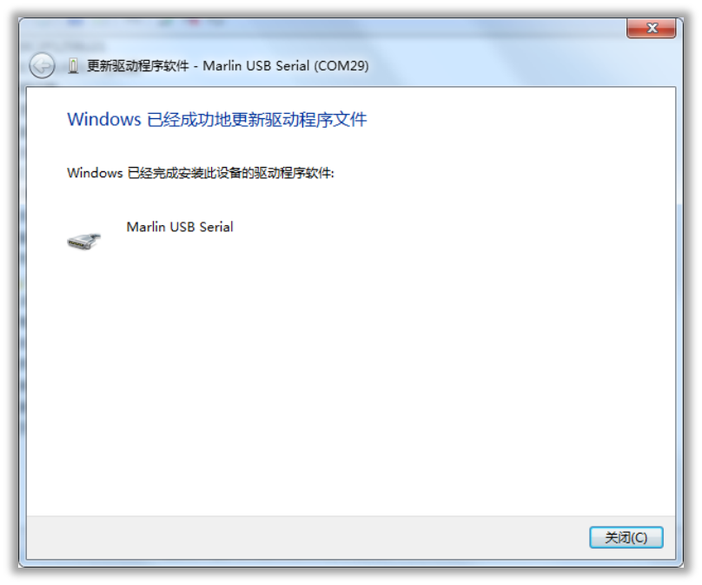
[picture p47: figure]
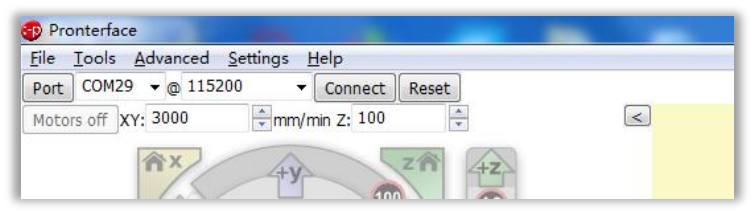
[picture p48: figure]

BIGTREETECH SKR V1.3 guide 2019 – V6 by Jupa Creations Page 17

If the install was successful, then the driver has been selected successfully. Remember the port number.

Open the Printrun/Pronterface online printing software as an example, select your com Port @115200, and then click Connect. Your COM port may be a different number.

On the right, you can see the printer is now online. This means that you have successfully connected to the printer. Now you can use your computer to control the printer

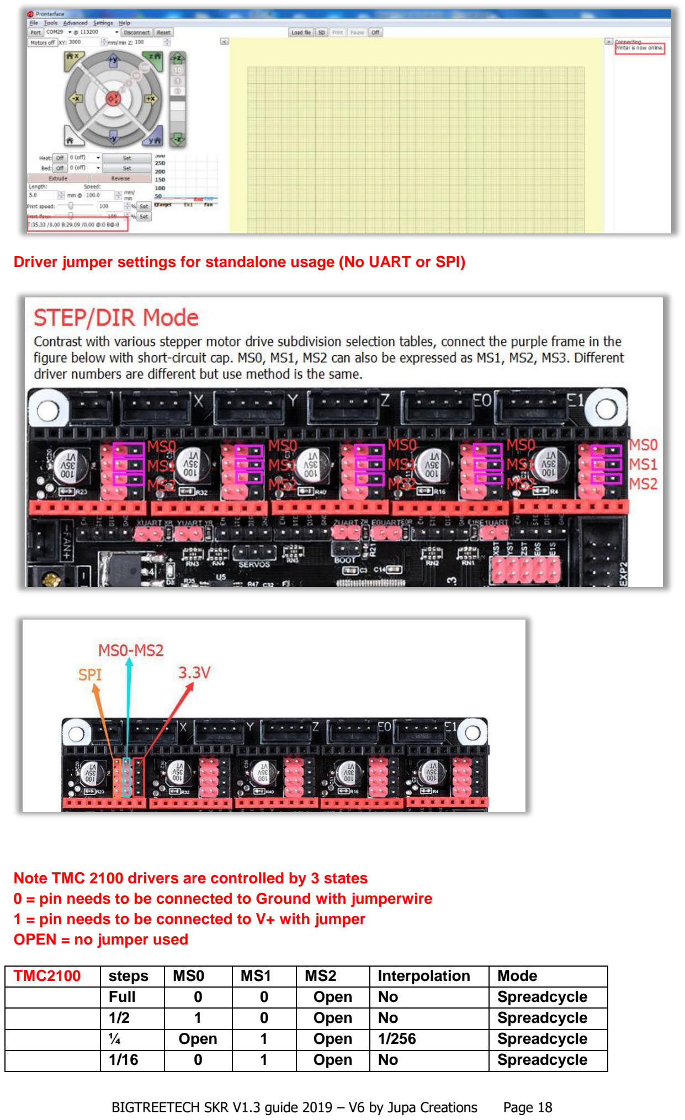
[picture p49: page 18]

BIGTREETECH SKR V1.3 guide 2019 – V6 by Jupa Creations Page 18

Driver jumper settings for standalone usage (No UART or SPI)

Note TMC 2100 drivers are controlled by 3 states
0 = pin needs to be connected to Ground with jumperwire 1 = pin needs to be connected to V+ with jumper
OPEN = no jumper used
TMC2100 | steps | MS0 | MS1 | MS2 | Interpolation | Mode
| Full | 0 | 0 | Open | No | Spreadcycle
| 1/2 | 1 | 0 | Open | No | Spreadcycle
| ¼ | Open | 1 | Open | 1/256 | Spreadcycle
| 1/16 | 0 | 1 | Open | No | Spreadcycle

BIGTREETECH SKR V1.3 guide 2019 – V6 by Jupa Creations | Page 19
1/4 | 1 | 1 | Open | No | Spreadcucle
¼ | Open | 1 | Open | 1/256 | Spreadcycle
1/16 | 0 | 1 | Open | 1/256 | Spreadcycle
¼ | 1 | Open | Open | 1/256 | Stealthchop1
1/16 | Open | Open | Open | 1/256 | Stealthchop1

Note TMC2208 drivers are controlled by 2 states
0 = no jumper needs to be placed between pink and black
1 = pin needs to be connected to V+ with jumper between pink and black
TMC2208 | steps | MS0 | MS1 | MS2 | Interpolation | Mode
| 1/2 | 0 | 0 | 0 | 1/256 | Stealthchop2
| ¼ | 0 | 1 | 0 | 1/256 | Stealthchop2
| 1/8 | 0 | 0 | 0 | 1/256 | Stealthchop2
| 1/16 | 1 | 1 | 0 | 1/256 | Stealthchop2

Note TMC 2130 drivers are controlled by 3 states
0 = pin needs to be connected to Ground with jumperwire
1 = pin needs to be connected to V+ with jumper between pink and black OPEN = no jumper used
TMC2130 | steps | MS0 | MS1 | MS2 | Interpolation | Mode
| Full | 0 | 0 | Open | No | Spreadcycle
| ½ | 1 | 0 | Open | No | Spreadcycle
| ½ | Open | 1 | Open | 1/256 | Spreadcycle
| ¼ | 0 | 1 | Open | No | Spreadcycle
| 1/16 | 1 | 1 | Open | No | Spreadcycle
| ¼ | Open | 1 | Open | 1/256 | Spreadcycle
| 1/16 | 0 | Open | Open | 1/256 | Spreadcycle
| ¼ | 1 | Open | Open | 1/256 | Stealthchop1
| 1/16 | Open | Open | Open | 1/256 | Stealthchop1

Drivers below only have 2 states

0 = no jumper needs to be placed between pink and black
1 = pin needs to be connected to V+ with jumper between pink and black
A4988 | steps | MS0 | MS1 | MS2 | Interpolation | Mode
| Full | 0 | 0 | 0 | No | None
| ½ | 1 | 0 | 0 | No | None
| ¼ | 0 | 1 | 0 | No | None
| 1/8 | 0 | 1 | 0 | No | None
| 1/16 | 1 | 1 | 1 | No | None
DRV8825 | steps | MS0 | MS1 | MS2 | Interpolation | Mode
| Full | 0 | 0 | 0 | No | None
| ½ | 1 | 0 | 0 | No | None
| ¼ | 0 | 1 | 0 | No | None
| 1/8 | 1 | 1 | 0 | No | None
| 1/16 | 0 | 0 | 1 | No | None
| 1/32 | 1 | 1 | 1 | No | None

BIGTREETECH SKR V1.3 guide 2019 – V6 by Jupa Creations | Page 20
ST820 | steps | MS0 | MS1 | MS2 | Interpolation | Mode
| Full | 0 | 0 | 0 | No | None
| ½ | 0 | 0 | 1 | No | None
| ¼ | 1 | 0 | 0 | No | None
| 1/8 | 0 | 1 | 1 | No | None
| 1/16 | 1 | 0 | 0 | No | None
| 1/32 | 1 | 0 | 1 | No | None
| 1/128 | 1 | 1 | 0 | No | None
| 1/256 | 1 | 1 | 1 | No | None
LV8729 | Steps | MS0 | MS1 | MS2 | Interpolation | Mode
| Full | 0 | 0 | 0 | No | None
| ½ | 0 | 0 | 1 | No | None
| ¼ | 1 | 0 | 0 | No | None
| 1/8 | 0 | 1 | 1 | No | None
| 1/16 | 0 | 0 | 1 | No | None
| 1/32 | 1 | 0 | 1 | No | None
| 1/64 | 1 | 1 | 0 | No | None
| 1/128 | 1 | 1 | 1 | No | None

Windows 10: Disable Signed Driver Enforcement

How can I install drivers that are not digitally signed?

Windows 10 enforces driver signatures by default. This can be disabled to install drivers that are not digitally signed. Use the following steps to disable driver signature enforcement.

1. Click the Start menu and select Settings.
2. Click Update and Security.
3. Click on Recovery.
4. Click Restart now under Advanced Startup.
5. Click Troubleshoot.
6. Click Advanced options.
7. Click Startup Settings.
8. Click on Restart.
9. On the Startup Settings screen press 7 or F7 to disable driver signature enforcement.

Your computer will restart and you will be able to install non-digitally signed drivers. If you restart your computer again the driver signature enforcement will be re-enabled.

If you are the creator of part of this document and you like your content to be removed please report.

This document is not created by BIGTREETECH!

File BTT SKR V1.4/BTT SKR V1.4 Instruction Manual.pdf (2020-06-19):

Shenzhen Big Tree Technology CO.,LTD .

## BIG TREE TECH

# BIGTREETECH SKR V1.4

# Motherboard Operating instruction

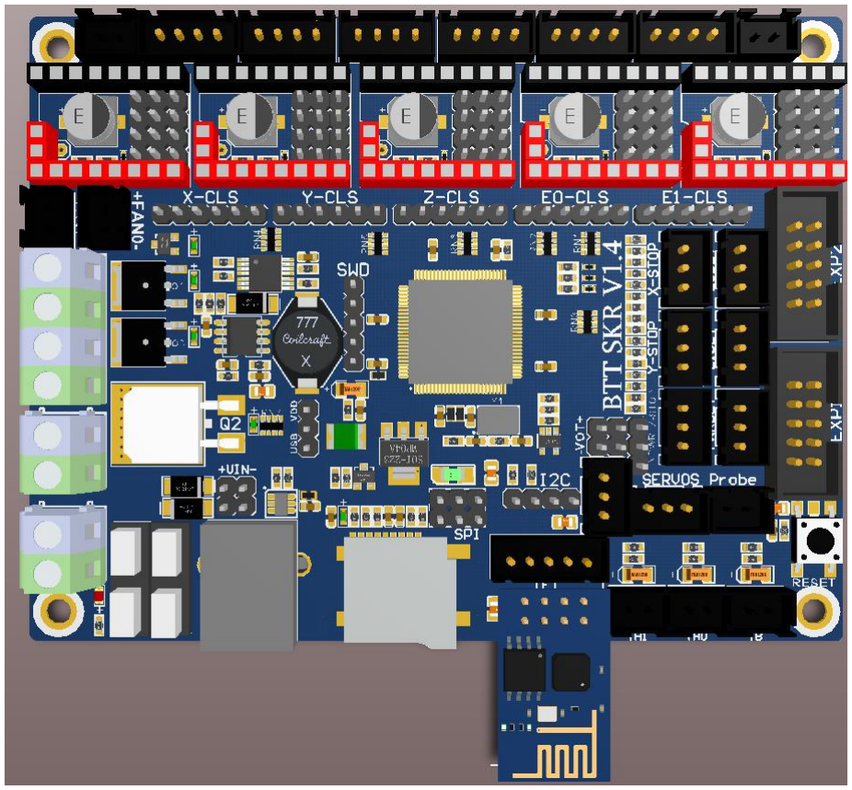
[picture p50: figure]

## BIG TREE TECH

# Ⅰ.Product Introduction

### BIGTREETECH SKR V1.4 motherboard is a 32-bit 3D printer

### motherboard optimized and upgraded by the 3D printing team of

### Shenzhen Big Tree Technology CO., LTD. for the deficiencies of V1.3

version, especially suitable for small and medium-sized printers.

### 1.SKR Motherboard Features:：

1）Using 32-bit main frequency 100MHz ARM level Cortex-M3 series LPC1768 main control chip, the performance has been greatly improved;
2）Equipped with highly modular and open source firmware Marlin2.0, which is convenient for users to DIY and secondary development;
3）Using dedicated power chip M6130, support 12-24V power input; 4）Support 2.4, 2.8, 3.5 inch color touch screen, support LCD2004 screen, LCD12864 screen；
5）Upgrade and configure the firmware through SD card, which is simple, convenient and efficient;
6）The SPI and UART working mode driven by the TMC driver, also having the DIAG pin, which eliminates complex wiring process and can be used by simple unplugging jumper cap;
7）Support Resume Printing While Power Off, Filament Break Detection, Automatic Shutdown After Printing and so on；
8）High performance MOSFET tube, better heat dissipation effect; 9）Using removable fuse makes the replacement process easier;
10）Reserved extended port SERVOS and Probe to support BL Touch;； 11）Support RGB light bar；
12）Use the power selection design to separate the USB power supply from the switch power supply, effectively avoiding the situation that the USB port of the computer is burnt out due to short circuit;
13）The special function interface uses the row needle with conspicuous color, which greatly reduces the error rate of wiring.
14）I2C, SPI and WIFI interfaces are reserved for convenience of DIY; 15）Closed-loop drive interface is reserved to reduce the trouble of plug-in switching module；
16）Double z-axis interface, eliminating the trouble of external drive expansion module;
17）The thermistor interface is protected by a bile capacitor pressurized resistor to enhance the resistance of the interface；
18）More fan interfaces: 1 way CNC fan, 3 way normally open fan;

## BIG TREE TECH

19）Plug-in external DC5V power supply module to supply power to TFT screen, BLtouch and Neopixel.

### 2.SKR Motherboard Parameters:：

Appearance size: 110*85mm
Mounting size: 102*76mm
Microprocessor: ARM Cortex-M3 CPU Input voltage: DC12V-DC24V 5A-15A
Logic voltage：DC 3.3V
WIFI module：ESP-01S
Motor driver: Support TMC5161、TMC5160、TMC2209、TMC2225、TMC2208、 TMC2130、ST820、LV8729、DRV8825、A4988 etc., independent external motor drive.
Driver working mode support: SPI、UART、STEP/DIR
Motor driver interface：X、Y、Z、E0、E1，5 way（Each has a closed loop drive interface) up to 256 subdivisions
Temperature sensor interface: TH0, TH1, TB, 3 channel 100K NTC Temperature sensor interface: TH0, TH1, TB, 3 channel 100K NTC (thermal resistance) Display：2.4、2.8、3.5 inch TFT（Support dual mode screen）、LCD2004、 LCD12864
PC communication interface: Square USB, easy to plug, communication baud rate of 115200
Expand the interface function support: Resume Printing While Power Off, Filament Break Detection, Automatic Shutdown After Printing, Automatic leveling, BL Touch
Support file format: G-code
Supported machine architecture: XYZ、delta、kossel、Ultimaker、corexy Recommended software: Cura、Simplify3D、pronterface、Repetier-host、 Makerware

# Ⅱ.SKR Motherboard Electricity:

After the SKR mainboard is powered up, the D5 red light in the lower left corner will go on, indicating normal power supply. The 5V SEL in the middle of the board is the power selection terminal；

1）When using USB to power the motherboard：

2）When using 12v-24v power supply：

## BIG TREE TECH

# Ⅲ.SKRMotherboard and Computer

# Connection

SKRmotherboard communicates with the computer through the [USB] interface. The computer needs to install the driver program first and then insert the motherboard into the computer to identify the port for data transmission. Without installing the driver, it is easy for the computer to fail to recognize the USB port.
Using the Marlin2.0 firmware, follow the tutorial for installation:

tutorial：https://www.dropbox.com/s/ppjfflhf3j5yzh2/MarlinV2.0%20SKRV1.1%20instruction.docx?dl=0driver：https://www.dropbox.com/s/a0k5idjmf4fn82f/lpc176x_usb_driver.inf?dl=0

# Ⅳ.SKR Motherboard and Interface

# Instruction

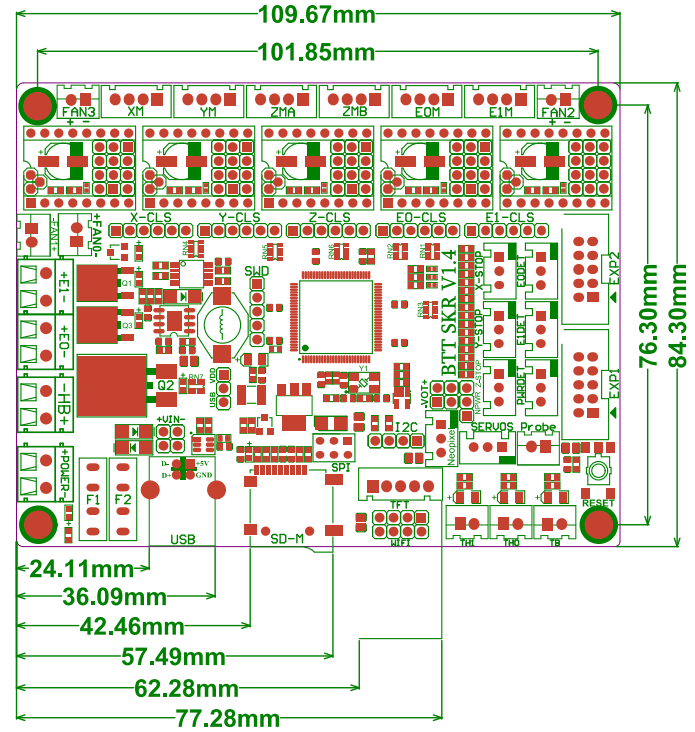
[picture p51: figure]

1. SKR Motherboard Size Diagram

## BIG TREE TECH

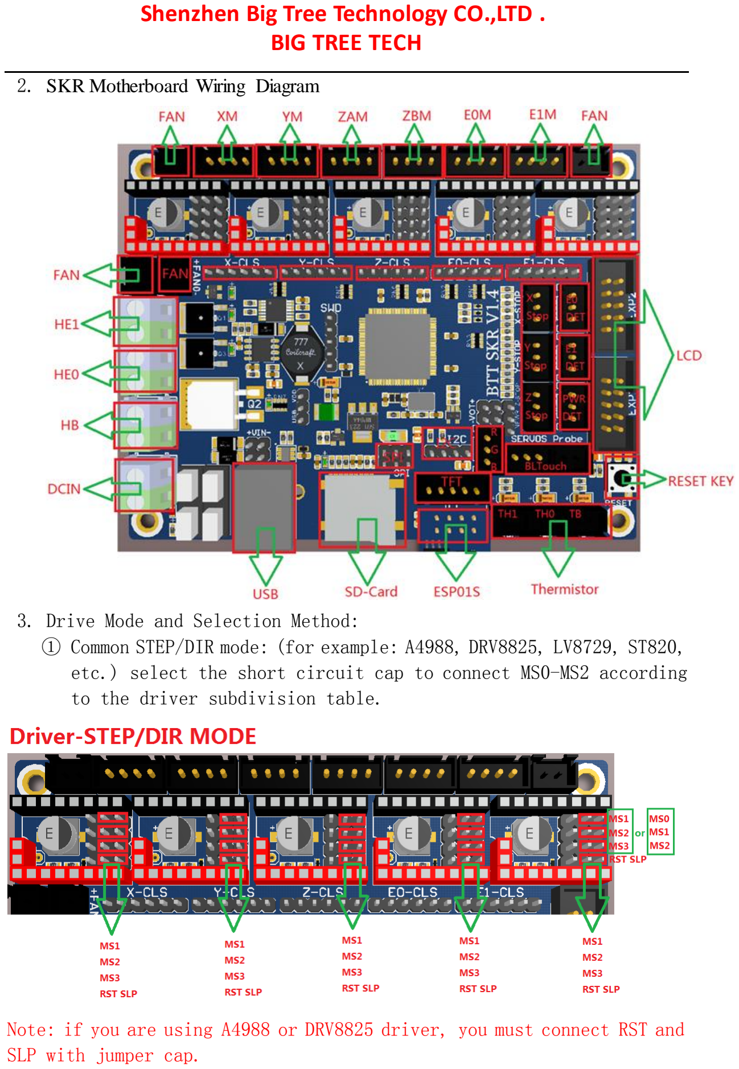
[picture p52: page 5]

2. SKR Motherboard Wiring Diagram
3. Drive Mode and Selection Method:
① Common STEP/DIR mode: (for example: A4988, DRV8825, LV8729, ST820, etc.) select the short circuit cap to connect MS0-MS2 according to the driver subdivision table.

Note: if you are using A4988 or DRV8825 driver, you must connect RST and SLP with jumper cap.

## BIG TREE TECH

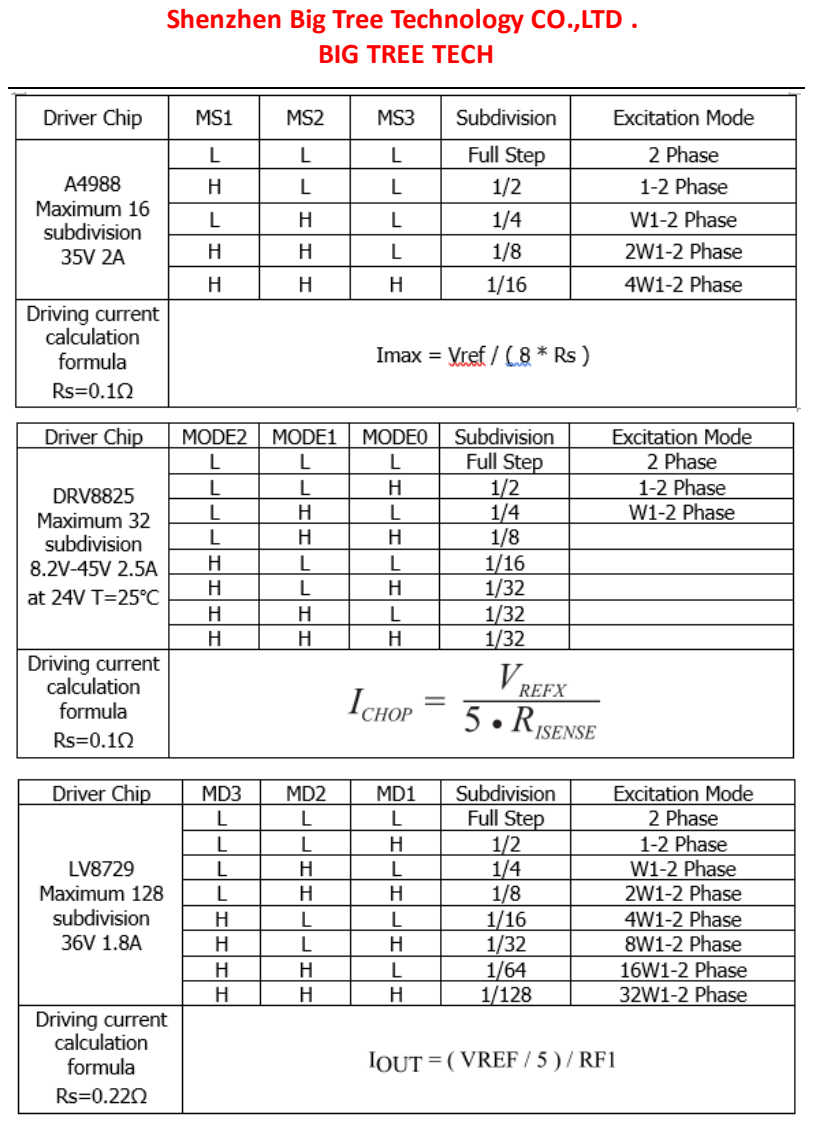
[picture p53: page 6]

## BIG TREE TECH

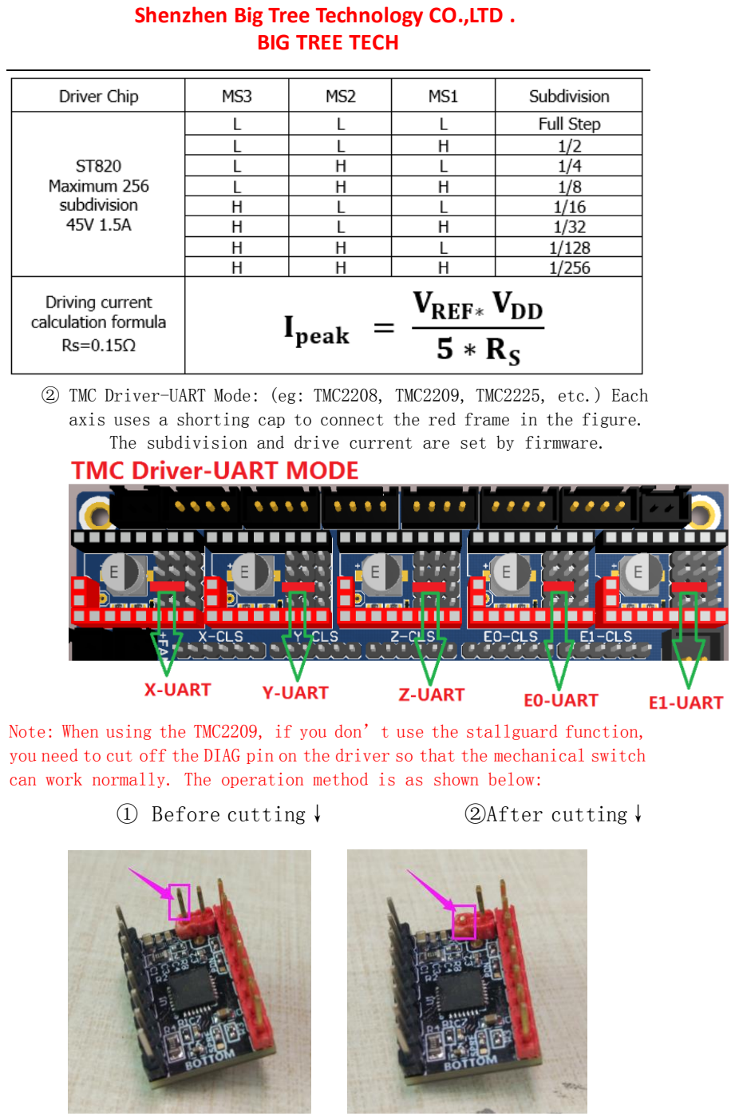
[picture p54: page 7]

② TMC Driver-UART Mode: (eg: TMC2208, TMC2209, TMC2225, etc.) Each axis uses a shorting cap to connect the red frame in the figure. The subdivision and drive current are set by firmware.

Note: When using the TMC2209, if you don’t use the stallguard function, you need to cut off the DIAG pin on the driver so that the mechanical switch can work normally. The operation method is as shown below:
① Before cutting↓ | ②After cutting↓

## BIG TREE TECH

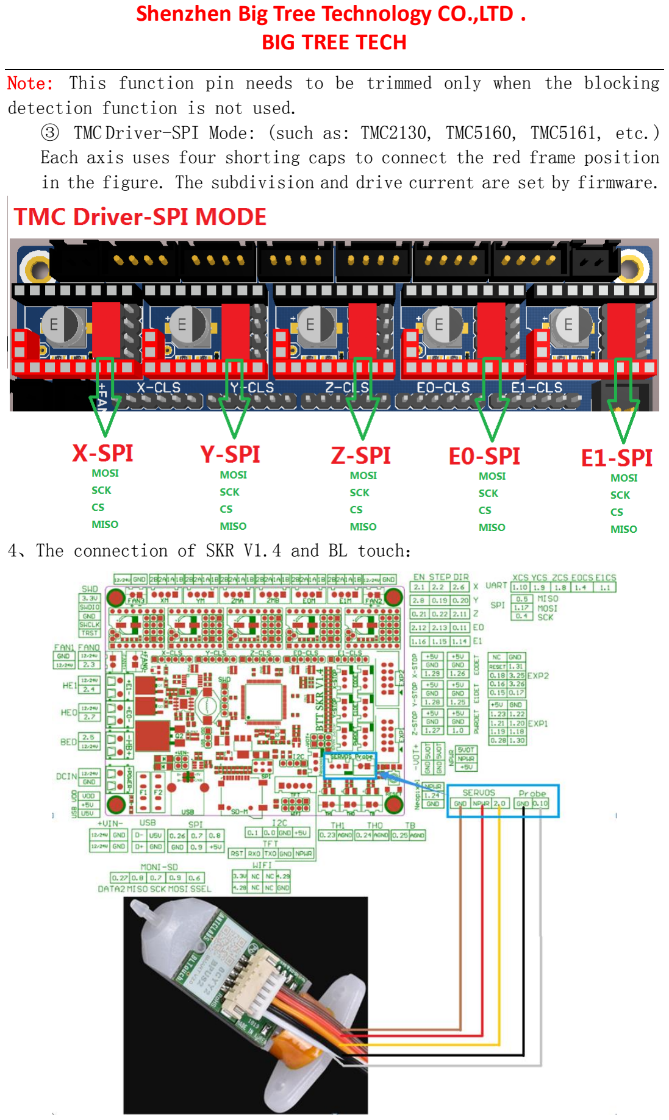
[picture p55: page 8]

Note: This function pin needs to be trimmed only when the blocking detection function is not used.
③ TMC Driver-SPI Mode: (such as: TMC2130, TMC5160, TMC5161, etc.) Each axis uses four shorting caps to connect the red frame position in the figure. The subdivision and drive current are set by firmware.

4、The connection of SKR V1.4 and BL touch：

## BIG TREE TECH

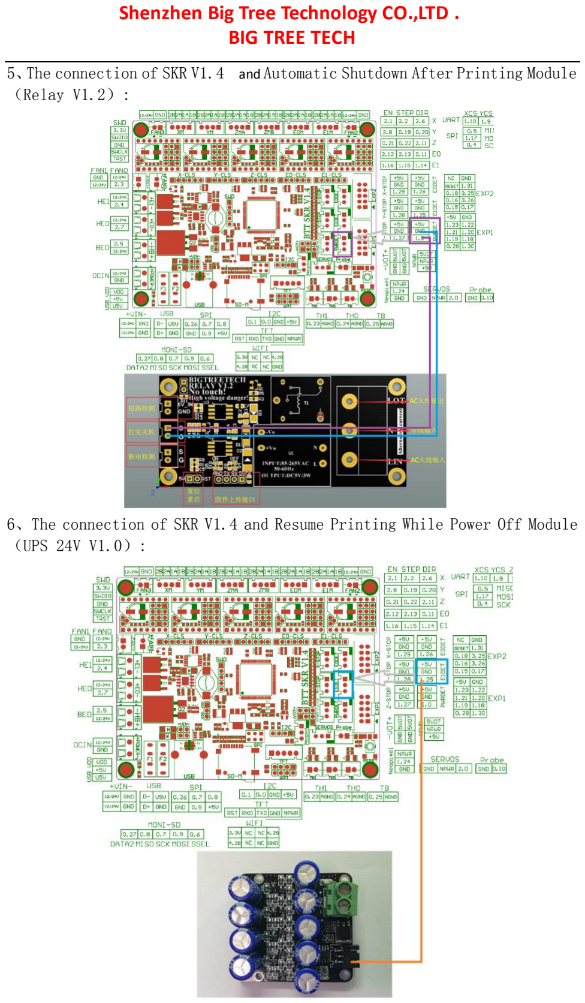
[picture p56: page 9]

5、The connection of SKR V1.4 and Automatic Shutdown After Printing Module （Relay V1.2）:

6、The connection of SKR V1.4 and Resume Printing While Power Off Module （UPS 24V V1.0）:

## BIG TREE TECH

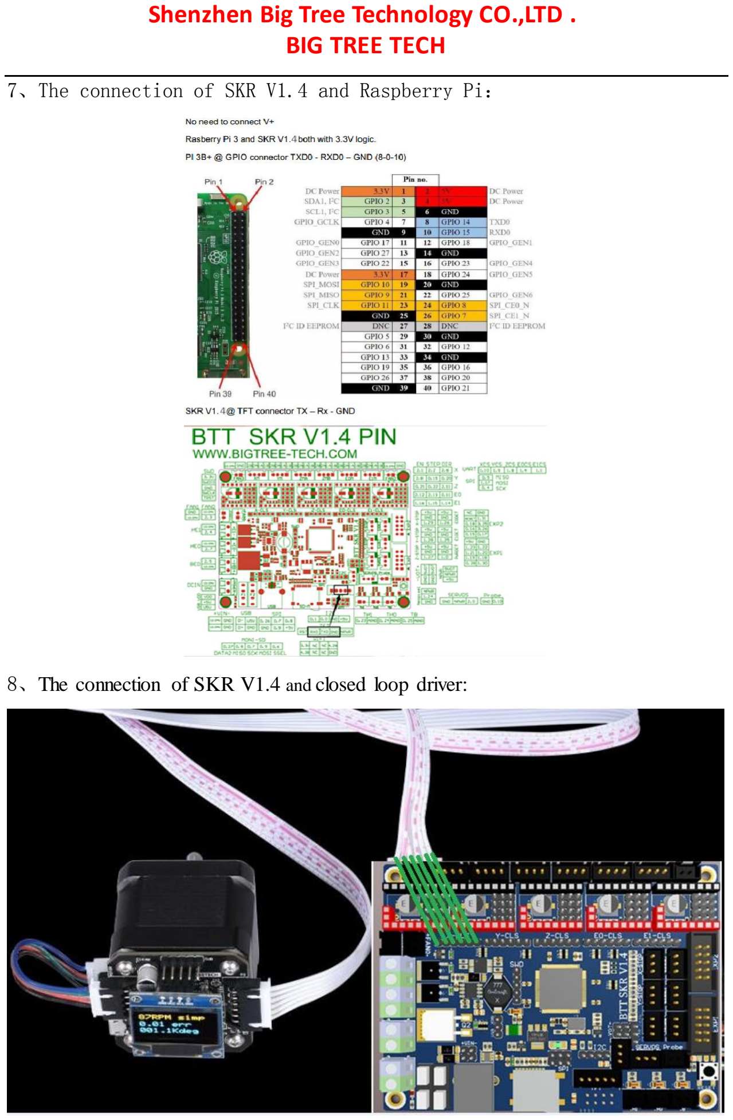
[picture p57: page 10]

7、The connection of SKR V1.4 and Raspberry Pi：

8、The connection of SKR V1.4 and closed loop driver:

## BIG TREE TECH

# Ⅴ.The firmware description of SKR

# motherboard

The factory motherboard is installed equipped with firmware for testing (model I3), which can be used directly or changed according to your own needs.
1. The Firmware Acquisition Method of SKR Motherboard:
Obtain by Ask customer service or technical personnel;
Download at our Company Open source website: https://github.com/bigtreetech
2.Marlin2.0 Firmware update method

After downloading our open source Marlin2.0 firmware, use Visual Studio Code to open the project to compile, then find the firmware.bin file, copy it to the SD card, and then reset the motherboard. For detailed steps, please refer to the tutorial:

https://www.dropbox.com/s/ppjfflhf3j5yzh2/MarlinV2.0%20SKRV1.1%20instruction.docx?dl=0

## Ⅵ.Notes：

## 1. The motherboard 5V SEL must connect VDD and +5V two pins

## before printing (that is, 12v-24v power supply must be provided

to the motherboard for printing);

## 2. The power of the hot bed connected to the motherboard must

## be less than or equal to 144W (that is, the thermal bed

## resistance is greater than 1Ω). If you want to use a high-power

## hot bed, you must connect an external hot-bed power expansion

board;

## 3. Firmware file names in SD card cannot be changed

## (including letter case)；

## 4. The wiring process and plug-in drive process must be

## BIG TREE TECH

## carried out under the premise of power failure. The power can

## be put on after checking the correct connection of the line and

## the correct insertion of the drive, so as to prevent the wrong

## connection line from burning the motherboard and driver and

## causing unnecessary losses；

## 5. To replace the configuration file, please backup the

## factory configuration file to record the pin number of each part

## of the chip, and then change the new configuration file!

### If you encounter other problems, please contact us. We will

### definitely answer your questions patiently. If you have any good

### suggestions on our products, please give us feedback. We will

### consider them seriously. Thank you for choosing BIGTREETECH

### products!

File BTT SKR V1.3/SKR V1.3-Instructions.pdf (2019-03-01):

Shen Zhen Big Tree Technology CO. ,LTD.

## BIG TREE TECH

# BIGTREETECH SKR V1.3

# Instructions

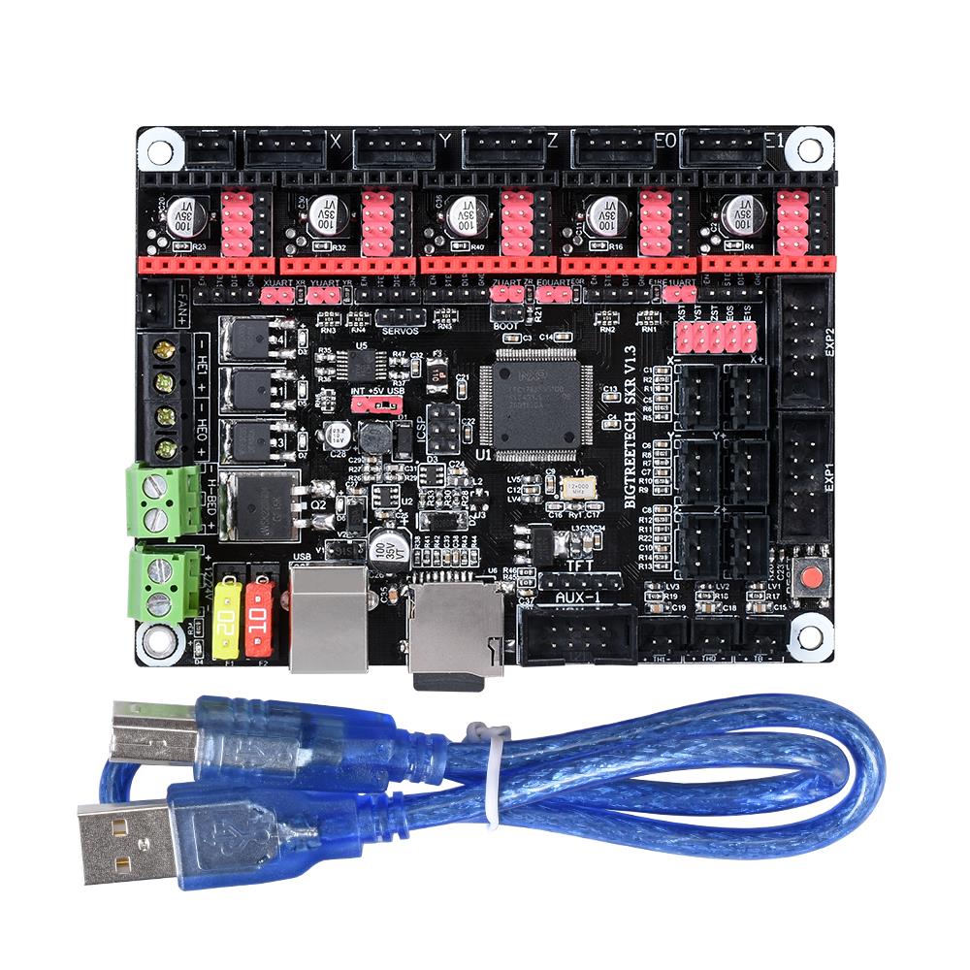
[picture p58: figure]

## BIG TREE TECH

# 一、Introduce

BIGTREETECH SKR V1.3 motherboard is R&D by Shen Zhen Big Tree Technology CO.,LTD. .The BIGTREETECH SKR V1.3 motherboard not only with a high cost-effective but especially suitable for small and medium-sized 3D printers.

## 1. SKR motherboard features:

1) Using 32-bit main frequency 100MHz ARM level Cortex-M3 series LPC1768 main control chip, the performance has been greatly improved;
2) Equipped with highly modular and open source firmware Marlin2.0 and Smoothieware, it is convenient for users to DIY and secondary development, and can avoid worries of not mastering the core code;
3)Marlin2.0 uses powerful development tools, Visual Studio Code integrated development environment: support online debugging, more helpful for product development and performance optimization, using C language development, low development threshold.
4) PCB board wiring is rigorous and beautiful, and specialized in heat dissipation optimization treatment;
5) the use of dedicated power chip, support 12-24v power input;
6) it can accept 24V input and reduce the hotbed current to 1/4 at the same power, effectively solving the heating problem of hotbed MOS tube;
7) Support 2.8-inch and 3.5-inch color touch screens, support 2004 LCD and 12864 LCD.
8) The system supports simplified Chinese, English and other languages, and can switch by itself;
9)Upgrade and configure the firmware through SD card, which is simple, convenient and efficient.
10)The SPI working mode of the TMC2130 driver and the UART working mode driven by the TMC2208,, which eliminates complex wiring process and can be used by simple unplugging jumper cap;
11)Support | Resume | Printing | While | Power | Off,Filament | Break
Detection,Automatic Shutdown After Printing and other functions.
12) High performance MOSFET tube, better heat dissipation effect;
13) The use of removable fuse makes the replacement process easier;
14) Reserved extended port SERVOS of PWM signal to support BL Touch;
15) Use the power selection design to separate the USB power supply from the switch power supply, effectively avoiding the situation that the USB port of the computer is burnt out due to short circuit;
16) The special function interface USES the row needle with conspicuous color, which greatly reduces the error rate of wiring.

## 2. SKR Motherboard Parameters:

Appearance size: 110*85mm

## BIG TREE TECH

Mounting size: 102*76mm
Microprocessor: ARM cortex-M3 CPU
Input voltage: DC12V-DC24V 5A-15A
Motor driver: support TMC2208, TMC2130, ST820, LV8729, DRV8825, A4988, can be independently external motor drive
Driver working mode support: TMC2130SPI, TMC2208UART
Motor drive interface: X, Y, Z, E0, E1, five (each has a reextendable interface), Up to 256 subdivisions
Temperature sensor interface: TH0, TH1, TB, 3 channel 100K NTC (thermal resistance)
Display: 2.8 "TFT, 3.5" TFT, LCD2004, LCD12864
PC communication interface: square USB, easy to plug, communication baud rate of 115200
Expand the interface function support: Resume Printing While Power Off,Filament Break Detection,Automatic Shutdown After Printing, Automatic leveling, BL Touch
Support file format: g-code
Supported machine architecture: XYZ, Delta, Kossel, Ultimaker, Corexy
Recommended | software: | Cura, | Simplify3D, | pronterface, | Repetier-host,
Makerware

# 二、SKR motherboard electricity:

When the SKR motherboard is electricity , the red light D4 in the lower left corner will light up, indicating that the power supply is normal. The middle of the board
5V SEL is the power selection end;
1) when using USB to power the motherboard, short circuit cap should be used to connect +5V and USB legs;
2) when using 12v-24v power supply, short circuit cap shall be used to connect +5V and INT pins;
Note: can be connected [12v-24v power], [USB] at the same time , the printing process must be connected with a short circuit cap +5V And INT.

## 三、SKR V1.3 Motherboard and Computer Connect

The SKR motherboard connects with the computer via the [USB] interface. After the driver is installed, the motherboard can be inserted into the computer to recognize the port for data transmission. Without the driver installed, it is easy for the computer to not recognize the USB port.
1. Smoothieware-usb-driver-v1.1 driver installation (Windows systems only)
The driver can be obtained from our open-source network; Https://www.dropbox.com/s/ighnj7oa2l0bm5g/smoothieware-usb-driver-v1.1.exe?dl= 0 (https://www.dropbox.com/s/ighnj7oa2l0bm5g/smoothieware-usb-driver-v1.1.exe?dl=0)
2. After installing the driver, connect the computer and SKR motherboard with USB

## BIG TREE TECH

cable.
Open the “Device Manager” of the computer to view the COM number to which the “smoothieboard USB Serial” asynchronous communication port belongs.

Note: When using smoothieware open-source firmware, since only Windows system drivers, the SKR board at this time can only be recognized by the Windows system port! ! !
3. If you are using Marlin2.0 firmware, follow the tutorial to install:

Tutorial: https://www.dropbox.com/s/ppjfflhf3j5yzh2/MarlinV2.0%20SKRV1.1%20instruction.docx?dl=0

Driver: https://www.dropbox.com/s/a0k5idjmf4fn82f/lpc176x_usb_driver.inf?dl=0

## 四、SKR V1.3 Motherboard and Interface

## Instruction

### 1. SKR Motherboard Size Diagram

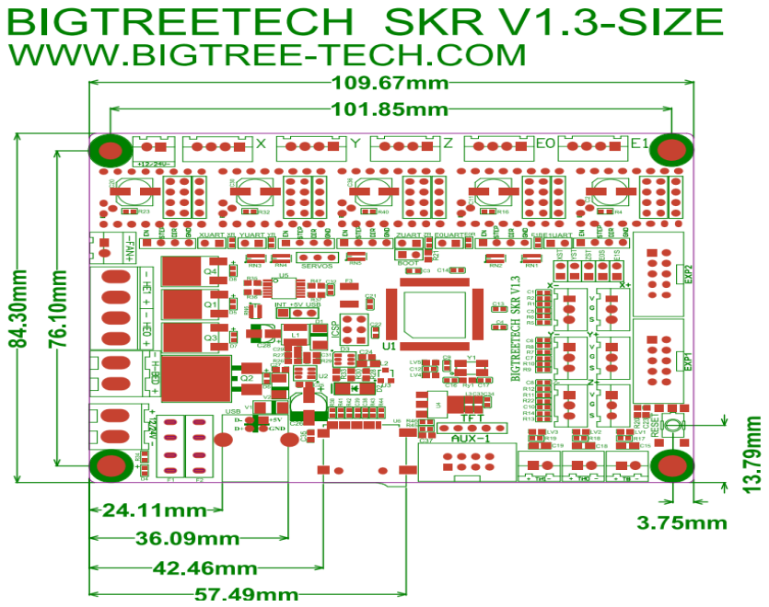
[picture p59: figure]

## BIG TREE TECH

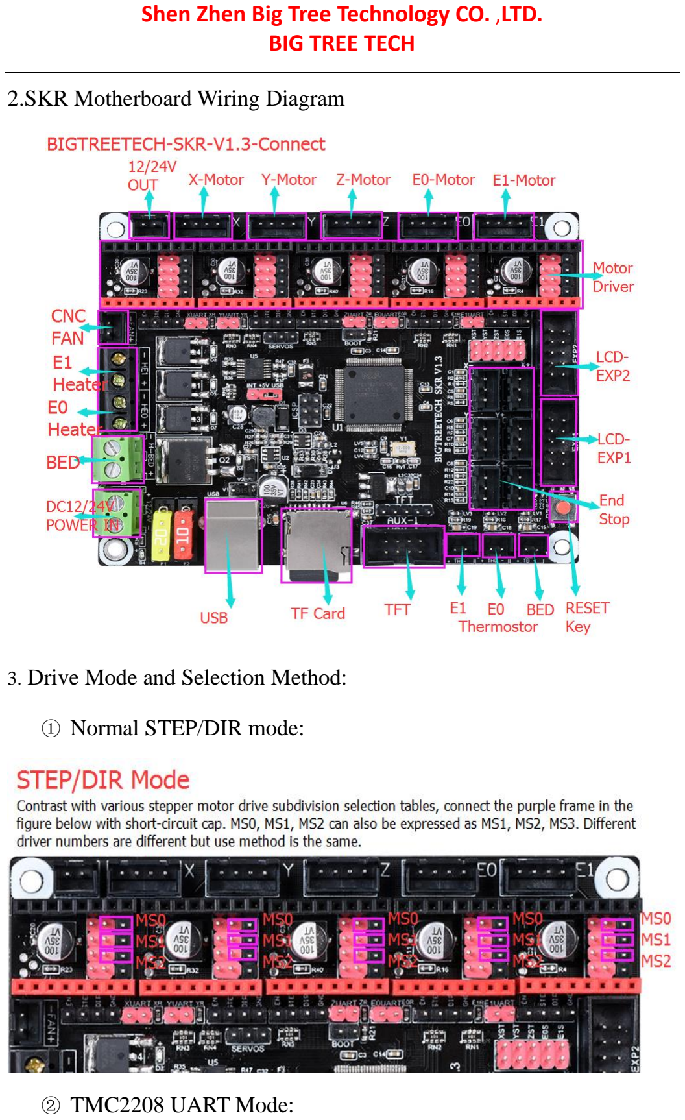
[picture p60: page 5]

### 2.SKR Motherboard Wiring Diagram

### 3. Drive Mode and Selection Method:

### ① Normal STEP/DIR mode:

### ② TMC2208 UART Mode:

## BIG TREE TECH

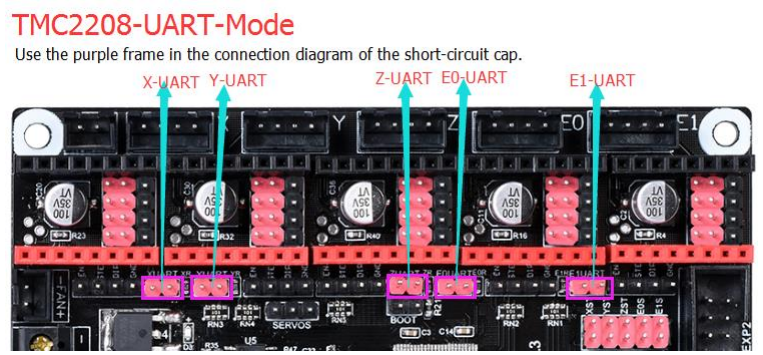
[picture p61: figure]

### ③ TMC2130 SPI mode:

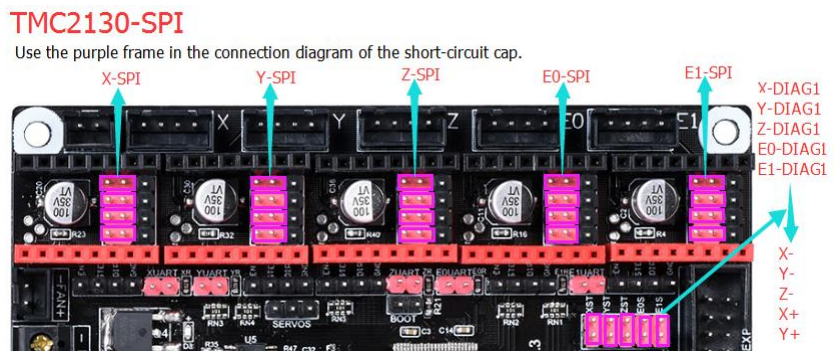
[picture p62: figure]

## 五、The firmware description of SKR motherboard

The factory motherboard is installed equipped with firmware for testing (model I3), which can be used directly or changed according to your own needs
1.The Firmware Acquisition Method of SKR Motherboard.
Obtain by Ask customer service or technical personnel ;
Download at our Company Open source website:
https://github.com/bigtreetech
2. Smoothieware Firmware update method
1）Choose the file suitable for your model in the downloaded firmware package to copy to SD Card Root directory，Include:
①Firmware: firmware.bin (Choose according to your model ) ②Configuration file config.txt(change your configuration by youself according your own needs)
Detailed functional options in the configuration file can be referred to the Open source Website:http://smoothieware.org/configuration-options

## BIG TREE TECH

Note: File name cannot be changed, firmware. bin must be lowercase!
2）Insert SD card into the main board SD card slot, re-energize or press the reset key, wait for about 10S.
After that, the update can be completed.
3. Marlin 2.0 firmware update method
After downloading our company's open source Marlin 2.0 firmware,open the project in Visual Studio Code,building it, then find the firmware. bin file, copy it to the SD card, and reset the motherboard.
For detailed steps, please refer to the tutorial: https://www.dropbox.com/s/ppjfflhf3j5yzh2/MarlinV2.0%20SKRV1.1%20instruction.docx?dl=0

# 六、Notes:

1. The 5V SEL of the motherboard must be connected with INT and + 5V pins before printing (that means there must using the 12V-24V power supply to the motherboard for printing.
2. The power of the hot bed connected to the motherboard must be less than or
equal to 144W (i.e. the resistance value of the hot bed is | above | 1Ω). If using
high-power hot bed , it must connected to the power expansion plate of the hot bed )

3.Firmware file names in SD Card cannot be changed (including both upper and l ower case letters);

4.The wiring process and the plug-in drive process must be carried out under the pr emise of power off. The power on can be started after checking the correct connect ion of the line and the correct insertion of the drive, so as to prevent the wrong con nection of the main board and drive from being burnt down and causing unnecessa ry losses.

5.If you want to replace the configuration file, please backup the factory configurat ion file to record the pin number of each part of the chip, and then make changes to th e new configuration file!

## BIG TREE TECH

# FAQ (Frequently Asked Questions)

Q: The computer does not recognize the SKR motherboard?

A: Check if the smoothieware-usb-driver-v1.1 driver is installed, you can downloadin g and installing it through the original URL, connect the power selection port jumper cap to USB and +5V.
and connect the USB cable to the computer and the SKR motherboard.

Q: After changing the configuration file, insert the motherboard, the firmware failed t o update successfully?

A: Check if the format of the firmware.bin file in the SD card is correct, also the file n ame should be lowercase

If you encounter other problems while using, please contact us, we will answer you scrupulous; if you have any good comments or suggestions for our products, pls feel free to inform us, we will carefully consider your comments or suggestions, thank you for choosing BIGTREETECH products, thank you!

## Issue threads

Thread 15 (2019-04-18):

SKR 1.3 with MKS2208 v1.1 TMC Connection Error (UART)

Brainc0re, 2019-04-18:
I got my board today. For testing, i connected one stepper (Z). according to the manual i removed all jumpers from the STEP/DIR headers and set them on the UART headers. But i always get a TMC CONNECTION ERROR on the display...

This is may current build:
https://drive.google.com/file/d/1NryYj-VFD_dcWFG64mShB-L8xsBiXHr1/view?usp=sharing

doggyfan, 2019-04-18:
I had this and found out the problem was today.

On the TMC2208 driver board you need to solder the PDN to the N.C pin next to it. The serial connection will then be correct.

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

Brainc0re, 2019-04-18:
Okay. I will try it in ~20 minutes. Thank you

Brainc0re, 2019-04-18:
Nope. Still "TMC Connection Error" on the screen

doggyfan, 2019-04-18:
Have you also soldered the UART pad option on your TMC2208 board ?

Brainc0re, 2019-04-18:
The board has separate jumpers for UART

https://github.com/bigtreetech/BIGTREETECH-SKR-V1.3/blob/master/SKR%20V1.3-Instructions.pdf Site 5/6

doggyfan, 2019-04-18:
I highly recommend using the protection diodes on each driver board to protect them from back EMF etc.

[https://www.aliexpress.com/item/5PCS-Ultra-Silent-Protector-Stepper-Motor-Driver-Motherboard-Plug-type-Silent-Stepper-For-3D-Printer-Driver/32864664427.html](url)

doggyfan, 2019-04-18:
Also, comment out this line on the configuration_adv.h file ..

`
//#define SOFTWARE_DRIVER_ENABLE
`

Brainc0re, 2019-04-18:
> Also, comment out this line in your configuration_adv.h file ..
>
> `//#define SOFTWARE_DRIVER_ENABLE`

If i define that, error still there and i cant control the stepper via "move axis Z" anymore

PapeJelly, 2019-04-19:
Check out their instructional video which also includes TMC2208 setup

**https://www.youtube.com/watch?v=oaXfXkPYHpw**

Brainc0re, 2019-04-19:
> Check out their instructional video which also includes TMC2208 setup
>
> [](**https://www.youtube.com/watch?v=oaXfXkPYHpw**)

With the help from Vanessa_E, author of [TMC2208 UART on BigTreeTech/BIQU SKR V1.1 and V1.3 Controllers](https://www.instructables.com/id/TMC2208-UART-on-BigTreeTechBIQU-SKR-V11-and-V13-Co/), we found out, that my MKS Drivers are not able to communicate via UART. I need some Fyetc v1.2 or TMC2208 drivers from Eryone.

doggyfan, 2019-04-20:
That's not true, I'm using them just fine with the extra soldered connection.

Brainc0re, 2019-04-20:
I dont have solderpads on my Stepper drivers and soldering the to pins in the middle has the same function as the jumper on the board.

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

doggyfan, 2019-04-20:
Can you not solder a thin wire from the chips UART pin to the N.C pin ?
It's a bit tiny but easy enough to do under a good magnifying glass.

Brainc0re, 2019-04-20:
Vanessa_E made this suggestion too. I have so many tools and stuff, but no magnification/microscope and such thin wire. According to the datasheet from trinamic, the solder pads are 0.25mm wide and have a pitch of 0.5mm. Thats too small for me for soldering. I will order some v1.2 which have UART.

Closed 2019-04-19.

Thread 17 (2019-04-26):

TMC2208 [TMC CONNECTION ERROR]

lospo, 2019-04-26:
I configured marlin and SKR1.3 to work in uart mode but i have the same message on the display.
The driver are BIGTREETECH TMC2208 SKU:UUU001758
The board is SKR V1.3, i follow the instruction here: https://www.youtube.com/watch?v=oaXfXkPYHpw
But i have the same message on display.

Attached a photo of my driver.

Here is the output of my M122:
`                X       Y       Z       E
Enabled         false   false   false   false
Set current     800     800     800     800
RMS current     1436    1436   1436     1436
MAX current     2025    2025    2025    2025
Run current     25/31   25/31   25/31   25/31
Hold current    12/31   12/31   12/31   12/31
CS actual       0/31   0/31     0/31    0/31
PWM scale   	0       0       0       0
vsense          0=.325  0=.325  0=.325  0=.325
stealthChop     false   false   false   false
msteps          256      256     256     256
tstep           0       0       0       0
pwm
threshold       0       0       0       0
[mm/s]          -       -       -       -
OT prewarn      false   false   false   false
off time        0       0       0       0
blank time      16      16      16      16
hysteresis
-end            -3      -3     -3       -3
-start          1       1       1       1
Stallguard thrs
DRVSTATUS       X       Y       Z       E
stst
olb
ola
s2gb
s2ga
otpw
ot
157C
150C
143C
120C
s2vsa
s2vsb
Driver registers:
X       0x00:00:00:00    Bad response!
Y      0x00:00:00:00     Bad response!
Z       0x00:00:00:00    Bad response!
E       0x00:00:00:00    Bad response!
Testing X connection... Error: All LOW
Testing Y connection... Error: All LOW
Testing Z connection... Error: All LOW
Testing E connection... Error: All LOW
ok`
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

doggyfan, 2019-04-26:
Have you solder bridged the option pads on the TMC2208 driver boards to connect the UART pin on the TMC2208 to the UART driver board pin ?

lospo, 2019-04-26:
I made no solder, I place jumpers in the board and attached these drivers.
I have no idea of what to solder/connect

doggyfan, 2019-04-26:
Try soldering these two little pads together on each of your TMC2208 driver boards ..

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

lospo, 2019-04-26:
I asked also to the supplier, and he give me that image as reference for soldering two pins.
Are the same or i am confused?
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

doggyfan, 2019-04-26:
oh ok, go with what they say. If that doesn't work try the other two pads.

lospo, 2019-04-29:
Nope, i soldered these pads but the trouble still remain.
And now its difficoult for me de-solder and solder the other two pads.
Do you think i could solder every three pads?
I send photos, please tell me if you see something  wrong.
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

doggyfan, 2019-04-29:
You soldered the pads BigTreeTech said to solder. Try soldering the pads I showed you instead.

pauleley, 2019-04-29:
You need to apply 12 or 24v for it to work

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

pauleley, 2019-04-29:
You need to apply 12 or 24v for it to work

MrG1981, 2019-05-08:
I have the same issue
the jumper on the driver is soldered and works properly with FTDI serial to USB
but not on skr 1.3 board powered by USB or 12v from power supply

lospo, 2019-05-15:
Hi, i've soldered the pads together (because i have not good skill) and now it works!
Thanks to all of you!

doggyfan, 2019-05-15:
BigTreeTech are telling people to solder the wrong two pads together :( .. it should be the other two.

stricktech, 2019-05-15:
hello, i have done the same thing, but i am getting tmc connection error.

i have soldered all 3 pads together, placed on skr 1.3 with the uart jumpers in place.
set firmware to TMC2208 and turned on TMCDEBUG.

i have my board and lcd at work right now, so cant test from 12 volt, powering from usb can give a tmc connection error?

lospo, 2019-05-15:
Yes, USB power is too low.
You need tre 12/24v power

stricktech, 2019-05-15:
Ok thanks, I'll reload the firmware and test it from my power supply when I get home.

Just to clarify something I wasent sure about or have heard differing information,

All jumpers should be removed besides uart?
(Black jumpers under driver, and red jumpers to the right side of board)

lospo, 2019-05-16:
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

I removed all, and it works. :D

LongLiveCHIEF, 2019-06-27:
> BigTreeTech are telling people to solder the wrong two pads together

No they're not. You can use either combination, or even solder all 3 pads together. You need to be applying the right voltage to the board in order for the the tmc2208 to allow current to flow.  The low voltage from your laptop/PC won't do the trick.

Peterg125, 2019-06-27:
Same exact problem. I'm replacing my Ender3's main board with SKR v1.3 from bigtreetech. Using 2208 drivers. Have pads soldered, have jumpers on the Uart pins on the board. connected to the 24v powersupply.
Important note:
My board came with a damaged capacitor on E0, so I switched the pin out defintions for E0 and E1 in code and am simply using E1 port for my extruder. Otherwise everything else is stock.

MakerThinking, 2019-10-16:
Hello, I have the same problem, I have tried all the options but I still have a tmc connection error on the lcd I have skr board v1.3 and tmc2208 silent stepper
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

hesham1967, 2021-01-19:
I think this has to do with software problem otherwise why I have TMC connection problem with Cura altimaker and Ideamaker but when I use control maker, I don’t have any problem with TMC

D4N1ELPAT, 2024-03-14:
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
Me funciono solde los 2 pats juntos y cuando conecte la placa funcionaba igual lo cheque en el pronterface con el comando m122 y funciono muchas gracias a todos

Closed 2019-05-15.

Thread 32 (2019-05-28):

SKR v1.3 PS_ON Pin

djice024, 2019-05-28:
I am building my own 3d printer, it is a delta printer so I decided to go for a 32-bit board. After some research, I concluded that the SKR 1.3 was the best option. With only one problem. I want to use an ATX power supply but can't find a PS_ON# pin on the SKR 1.3. Is there any way I can assign a PS_ON# pin or cant this board do this? Thanks for the help in advance.

doggyfan, 2019-05-28:
Try adding (Y_MAX pin as an example) ..

```cpp
#define PS_ON_PIN    P1_26
```

it ought to work OK.

The SKR 1.3 board is kind of short of pins, which is probably why no one has added the pin (don't know).
But BigTreeTech could have made more physical pins available. For a start, the CPU has 2 pins which aren't used at all (P1.0 and P0.26), you could solder to them if you're able. Then there are the 5 software UART Tx pins that could have had a pin header for the user to use as they so wish. And then they could also have put a pin header for the SPI motor lines (MOSI, MISO and SCK), though you can get to them under the driver boards.

djice024, 2019-05-29:
Yeah, the SKR 1.3 does have some flaws. I still feel it is better than just a RAMPS with a 32-bit controller. Doesn't the PS_ON need a connection to ground to turn on? And where will I be able to input the 5v? Thanks for the help.

doggyfan, 2019-05-29:
Not sure what you mean PS_ON needs connection to ground ?
The PS_ON pin will be an output pin from the board, How you connect it to your PSU will depend on the PSU's needs.

To feed +5V to the board, see the attached image ..

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

djice024, 2019-05-29:
The transistor would be between the PSU's PS_On pin and ground, controlled by the SKR 1.3, Right? the power makes sense. Thanks a lot.

doggyfan, 2019-05-29:
You've got three options really ..

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

A bit of an over-kill but you could just buy a little board to go between such as ..

https://www.ebay.co.uk/itm/3-20V-Mosfet-MOS-Transistor-Trigger-Switch-Driver-Board-PWM-Control-Module-CDUK/382886645254

djice024, 2019-05-29:
I'll try that out, Thanks.

Nonametruck, 2019-06-02:
If you are using the MKS tft there are pins there right?

djice024, 2019-06-02:
That's for the MKS PWC and you'll still need a PS_ON pin. This was for an ATX power supply.

djice024, 2019-08-25:
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

I have been doing some experimenting. I ended up using an NPN transistor. I tried using the resistor config you posted, but it didn't seem to work with that. It did work without the pullup resistor so I assume the board has a built-in one. I ended up using the BLtouch pin. I wanted to thank you as you helped out an immense amount. I attached of my pins.h and a pic of the printer.
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

leonyd0823, 2019-08-26:
Buenos días estoy tratando de poner unas tiras LED en esta placa skr v1.3 pero en realidad no se de donde tomar los pines ni cuales serían los más adecuado. Tanto para una tira LED RGB que una tira LED digital. La verdad busco un poco de información sobre este tema y un poco de ayuda muchas gracias el objetivo es poder controlar las tiras LED con la placa según el estado de la impresión.

djice024, 2019-08-26:
https://github.com/bigtreetech/BIGTREETECH-SKR-V1.3/issues/63

djice024, 2019-08-26:
> Buenos días estoy tratando de poner unas tiras LED en esta placa skr v1.3 pero en realidad no se de donde tomar los pines ni cuales serían los más adecuado. Tanto para una tira LED RGB que una tira LED digital. La verdad busco un poco de información sobre este tema y un poco de ayuda muchas gracias el objetivo es poder controlar las tiras LED con la placa según el estado de la impresión.

https://github.com/bigtreetech/BIGTREETECH-SKR-V1.3/issues/63

djice024, 2019-08-26:
> Buenos días estoy tratando de poner unas tiras LED en esta placa skr v1.3 pero en realidad no se de donde tomar los pines ni cuales serían los más adecuado. Tanto para una tira LED RGB que una tira LED digital. La verdad busco un poco de información sobre este tema y un poco de ayuda muchas gracias el objetivo es poder controlar las tiras LED con la placa según el estado de la impresión.

https://github.com/bigtreetech/BIGTREETECH-SKR-V1.3/issues/63

oxcxsxixbxaxn, 2019-09-16:
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

@djice024
So which of the 5 scenarios did you use?  I have a the components handy, but did you use the NPN only? and neither of the resistors shown?
Oh, the NPN is BC547, I think that is still appropriate, right?
Thx

Closed 2019-08-25.

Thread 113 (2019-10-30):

There are no resistors on any gate of power MOSFETs

ElectroAaron, 2019-10-30:
Driving directly power MOSFETs from MC74HCT125A without limiting resistors may damage the chip. A closer look at the [datasheet](https://www.onsemi.com/pub/Collateral/MC74HCT125A-D.PDF), reveals that maximum output current is ±35mA for each buffer output pin.

karabas2011, 2019-11-04:
So what conditions cause possible fail?

Pixel-Soup, 2020-01-30:
It shouldn't be an issue.  The fet gate looks like a capacitor to the driver whose ON resistance will limit the peak current during each pwm cycle.

ElectroAaron, 2020-01-31:
Yeah sure! It does make sense, I wasn't taking into account the own internal RDSon of the MC74HCT125A. Sorry for my mistake. Issue is close.

Closed 2020-01-31.

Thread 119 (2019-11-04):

DRV8825 not working on SKR1.3 for 1 driver(E0)

legojedidev, 2019-11-04:
So I use an Anet a8 but recently my board caught on fire. I decided to upgrade to an SKR 1.3 and bought 5 drv8825 stepper drivers. Everything works fine except for my E0(E1 is being used for my other z-axis). My E0 motor gets current, but it barely moves. Any idea why this may be happening? I am running Marlin 2.0 and can upload my configuration files later. Also I can't get my LCD 2004 to work. Any help is appreciated!

Tomthi, 2019-11-06:
Have you tried adjusting the vREF for that stepper driver? They may be set too low. I had issues with the voltages and after adjusting them performance was much better.

legojedidev, 2019-11-06:
I just figured out that the driver itself was causing a short

erberru70, 2019-11-29:
> Así que uso un Anet a8 pero recientemente mi placa se incendió. Decidí actualizarme a un SKR 1.3 y compré 5 controladores paso a paso drv8825. Todo funciona bien, excepto mi E0 (E1 se está utilizando para mi otro eje z). Mi motor E0 recibe corriente, pero apenas se mueve. ¿Alguna idea de por qué esto puede estar sucediendo? Estoy ejecutando Marlin 2.0 y puedo cargar mis archivos de configuración más tarde. Además, no puedo hacer que mi LCD 2004 funcione. Cualquier ayuda es apreciada!

hola , como conseguiste cargar marlin 2.0 en la placa skr v1.3, por que a mi no para de darme error al compilar marlin con vscode

Closed 2019-11-06.

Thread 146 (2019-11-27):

Z_Min always triggered (

fineobjetcs, 2019-11-27:
Hi ! I have this issue
At start all be ok! Z_Min works as Z_Probe fine, but three days ago Z_Min starts always triggered. I try to change firmware (Marlin20bugfix, smoothiware), change settings(invert ZMIN Probe etc), play with pullup, but nothing happens, i try this with and without wires and sensor.
What wrong ? May it be electrical error ? How i check the PIN directly ? Maybe from arduino IDE ? With simple code ? PIN 1_25 is analog or digital ?

fxh1357, 2019-11-28:
"Three days ago" sounds like a limit switch connected as normally closed, thus a broken wire or disconnected switch would result in a 'TRIGGERED' state

oldman4U, 2020-08-27:
Close this ticket or reply.

Closed 2020-09-02.

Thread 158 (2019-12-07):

SKR V1.3 with TFT35 and Marlin2.0 issue

ROL1978, 2019-12-07:
Hi!
I have problem with BTT SKRv1.3 board and BTT TFT35 display. Display say "No printer attached!". Build and upload work just fine, but after reboot it still say "No printer attached!".
Funny (really not so funny...) thing is that worked yesterday perfectly! Today I put my printer on and after that I can't get connect board to display.

I have try this:
#define SERIAL_PORT -1
#define SERIAL_PORT_2 0
#define BAUDRATE 115200

 and this way:
#define SERIAL_PORT 0
#define SERIAL_PORT_2 -1
#define BAUDRATE 115200

and both will build well but no make connect between printer and tft. Every time before buil I have delete old build and libdebs files.

Other hardware in board has TMC2208 drivers and BL-Touch sensor. Marlin 2.0 firmware is bigtreetech version.

ROL1978, 2019-12-07:
I have also tryed other SD-card as well.

ROL1978, 2019-12-07:
TFT is TFT35-V2.0

ROL1978, 2019-12-07:
Okay!!! I have solve it! If anybody have same probem then probably only  you have to do is press the printer TFT display "Menu" -> "Settings" -> and then press "Disconnect" icon. Then display give message "Now you can control the printer by your computer!"  Thats it. I can't understand why that needed. Only I turn power off yesterday and today it wasn't work anymore. But this simple task fix my case problem! I hope this will help somebody who have similar problem.

Closed 2019-12-07.

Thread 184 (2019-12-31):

SKR v1.4 - Schematic diagram is missing

bianchifan, 2019-12-31:
see title

GadgetAngel, 2020-01-25:
Where us the Schematic diagram for the SKRV1.4.  You can not expect us to believe that the LPC1768 chip and the LPC1769 chip are the same.  I really would like to see where each of the pins are coming from the LPC1769 chip. Please publish your schematic diagram for LPC1769 (SKR V1.4 Turbo) like you do for the LPC1768 (SKR V1.3)

MowMoney, 2020-01-25:
> Where us the Schematic diagram for the SKRV1.4. You can not expect us to believe that the LPC1768 chip and the LPC1769 chip are the same. I really would like to see where each of the pins are coming from the LPC1769 chip. Please publish your schematic diagram for LPC1769 (SKR V1.4 Turbo) like you do for the LPC1768 (SKR V1.3)

NXP Semiconductor, the people that make the chip, show the pin layout for the chip is identical. They have a very detailed pdf available if you care to research this for yourself.

GadgetAngel, 2020-01-26:
> > Where us the Schematic diagram for the SKRV1.4. You can not expect us to believe that the LPC1768 chip and the LPC1769 chip are the same. I really would like to see where each of the pins are coming from the LPC1769 chip. Please publish your schematic diagram for LPC1769 (SKR V1.4 Turbo) like you do for the LPC1768 (SKR V1.3)
>
> NXP Semiconductor, the people that make the chip, show the pin layout for the chip is identical. They have a very detailed pdf available if you care to research this for yourself.

OK, if that is the case then why do I see differences in the pins files.  For example here is my screen shot.  The file opened on the LEFT is the SKRV1.4 pins file, the file opened on the RIGHT is the SKRV1.3 pins file.   THIS is why I want to see the schematic.  If the pinout on each chip is exactly the same then why the different pin numbers on these items?  I just downloaded the Marilin-bugfix-2.0.x today.  If you could help me understand the difference I would be very grateful
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

MowMoney, 2020-01-26:
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

I see your point. And I honestly have no answer for this. I am no expert on this subject by any stretch. I had simply looked into the chip as I was curious about the differences, which I understood to be clock rate.

My guess is the chips have the same basic pin layout and the boards are designed differently. I don’t believe the chip cares what pin does what, but more the internal geometry of the board dictates which pins are assigned to what function.

michielbaird, 2020-01-29:
I am very interested on this. The schematic is the best way to see if there are adequate, protections build into the circuit and how it can interact with external components, a pinout diagram is not sufficient. For example what is the size of the reference resistors used on the ADCs, are there additional ADC pins available etc.

DeviousPenguin, 2020-01-29:
I'd be interested in a schematic also, as I may look at using this board as a part of a 36v setup.

michielbaird, 2020-03-03:
On the Facebook group I've now seen several boards that have burned. It's difficult to diagnose these issues without having access to the schematic. Im assuming there is a reason this is being withheld.

asdmin, 2020-03-09:
dup to https://github.com/bigtreetech/BIGTREETECH-SKR-V1.3/issues/184

DeviousPenguin, 2020-03-12:
> On the Facebook group I've now seen several boards that have burned. It's difficult to diagnose these issues without having access to the schematic. Im assuming there is a reason this is being withheld.

It seems the SKR V1.3 can be run with 36V for the motors if the 35V caps are replaced, but for now I'm sticking with 24v as I don't want to burn my board.

Do you have a link to the burned boards, I'm interested in seeing what *not* to do! :)

bianchifan, 2020-03-12:
Thank you!

laserbudd, 2020-03-14:
Hi, I am really a nooby in this 3D printing, but I have a question about this board (SKR 1.4 Turbo).
I have a modded Anet A6 (A8, supposedly) that has a Anet V1 board on it.  I am wanting to upgrade it to the SKR 1.4, and be able to use it for learning on, as I am eventually want to build a "cube" printer.
Can anyone possibly give me a wiring diagram so I can do this?
Thanks for any help I can get and, if I am making an error posting in this thread, would a Moderator please tell me?

Closed 2020-03-12.

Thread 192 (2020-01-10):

TMC2209 and SKR 1.4 Turbo

delwinbest, 2020-01-10:
Hi Team,
I've spent a few hours trying to get the TMC2209 to register on the SKR 1.4 TURBO. I've tried 5 different drivers, and have followed your instructions. I've also tried your supplied firmware, and I have my own. Each time I get 'bad response'.

Please help! I currently use these drivers in a MKS board without any trouble.
My current config can be found here: https://github.com/delwinbest/Marlin_BIBO2_touch_dual/tree/btt_skr_v1.4_turbo

Attached is a photo of my jumper connection. I can't find anything else I can try. Could you perhaps provide a schematic for the Turbo board?

Photo of Jumpers: https://github.com/delwinbest/Marlin_BIBO2_touch_dual/blob/btt_skr_v1.4_turbo/jumpers.png

delwinbest, 2020-01-11:
Ignore. Found the problem: The board must be powered by main supply to test TMC drivers. Not USB. 5 hours lost :D

wallen83, 2020-01-27:
so you can't check status in pronterface with only usb power? I spent 4 hours with it yesterday ...
also has problems with tmc2209 and sensorless homing .. it does not want to stop. can't find what's wrong. are you running sensorless homing?       (skr v1.4 board)

Fuglys, 2020-01-28:
waw thanks that can be the problem why M112 gave a kill

delwinbest, 2020-01-29:
@wallen83 that was my experience. I could not get it to work until I powered up the board with my 12/24V Supply. Also lost hours trying.
I'm using sensor-less homing which works well.

thetechy2, 2020-02-04:
> also has problems with tmc2209 and sensorless homing .. it does not want to stop. can't find what's wrong. are you running sensorless homing? (skr v1.4 board)
1.4 turbo 2209 trouble with sensorless homing here please reply if youve found anything

wallen83, 2020-02-04:
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

yes i use sensor less on my skr1.4/TMC2009 UART.   I had removed // on the wrong sensor less homing in marling fw.  I had removed it on sensor_less_probing  🙈

you have all the pins left? (on TMC2009)

thetechy2, 2020-02-04:
> you have all the pins left? (on TMC2009)

yeah all the pins are there. when i try to home it, it just fails and halts the printer

drphil3d, 2020-04-20:
HEY GUYS! MAKE SURE TO CUT the pin on the Z stepper driver if your using tmc2209 RTFM!

drphil3d, 2020-04-20:
Also, I learned this one the hard way, if you enable sensorless homing on Z axis, the pins file changes the input from Z-STOP to PWR-DET port.

Closed 2020-01-11.

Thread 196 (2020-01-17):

USB (mostly) stopped working

rally25rs, 2020-01-17:
My SKR 1.3 had been working fine for a couple days, with USB to both a Macbook and a Rasp Pi (octopi).

Suddenly it disconnected from OSX and ever since has been exhibiting weird behavior:

* If I plug it into any USB port on the Rasp Pi, it is not recognized (`dmesg` and `lsusb` show nothing conected). This had been working prior.
* If I plug it into my Macbook on the same port where it had been working, the board does not register.
* If I plug it into the _other_ USB port on my Macbook, it shows up as a drive (as it should) and I can see the SD card, however Printrun/Pronterface can't connect to it as a printer.
* The board does power up, on both 5v USB and 12v external PSU modes and the red light is on.
* The board will reflash itself if you put new firmware on the sd card (moves firmware.bin to firmware.cur as you would expect)

Things I checked:
* Testing with a meter, the data pins of the USB port do have continuity back to the pins of the main processor chip.
* There is no resistance between R30 and the processor chip, and R33 and the chip, so the leads appear to be intact.
I tried a different USB cable. Same behavior.

What really throws me for a loop is that it shows up as a drive on one USB port and not the others, but even when it shows up as a drive, it doesn't work as a printer.

I also tried connecting my Pi over the UART (to the Aux1 plug on the SKR) but that doesn't seem to work either. I can never get Octoprint to connect.

Using bugfix 2.0.x branch of Marlin (not the BTT fork) and the serial ports are set appropriately
```
#define SERIAL_PORT -1
#define SERIAL_PORT_2 0
#define BAUDRATE 115200
```
(and also didn't change between when this was working and stopped working)

I'm assuming something with the board or processor is toast, but... anyone have any thoughts on troubleshooting?

Marsman1970, 2020-01-18:
Well  i have  my serial port 2 set to 1  that worked better for me for some reason maybe worth trying.
Michael

Marsman1970, 2020-01-19:
Also if you have temperature sensor problems the usb stops working.

rally25rs, 2020-01-19:
I tried flipping to

#define SERIAL_PORT 2
#define SERIAL_PORT_2 -1

which is the default for the SKR minis
https://github.com/MarlinFirmware/Marlin/blob/2.0.x/config/examples/BigTreeTech/SKR%20Mini%20E3%201.2/Configuration.h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

Interestingly my USB seems to be working again, even though I'm 99% sure that `-1` is the USB, and it was working fine as `SERIAL_PORT -1` before 🤷‍♂

So that gets me somewhere at least... I'd still like to figure out how to get my Pi connected over the serial pins on the AUX1 port.

I've also yet to find any actual docs on what the numbers for the serial port are... I've seen it listed that `0` is the AUX1 port, but as linked above, the example for the SKR minis are `2`, and you said you are using `1`... It'd be nice to know what the actual values represent 😕

> Also if you have temperature sensor problems the usb stops working.

yeah I had noticed from a previous wiring mishap that if a limit switch is shorted then it halts the board too, so I have every connection disconnected while I was testing this. Actually the board is out of the printer just laying on the workbench on the static bag it came in with nothing but USB and the AUX1 pins for Gnd, TX, RX connected.

Closed 2020-01-19.

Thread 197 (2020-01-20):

Bigtreetech SKR V1.4 Turbo usb connection problem

Remohpant, 2020-01-20:
Hi, recently bought the skr 1.4 turbo and trying to upload marlin firmware 2.0.x. Issue is that pc doesnt recognise the usb connection. it fails after 1min of powering up the board.
Does enaybody else encounter the same?

kaibs, 2020-01-20:
Do you have anything connected to the board?

I had a similar problem and in my case the reason for having the board crashing all the time was a damaged thermistor. It seems like if a sensor (endstops should cause this problem too) is shorted, marlin is prevented from booting and the board somehow kills it's USB connection.

Remohpant, 2020-01-20:
Thank you very much. It was thermistor. Once disconected them it worked.

   Στις Δευτέρα, 20 Ιανουαρίου 2020, 9:42:06 π.μ. EET, ο χρήστης kaibs <notifications@github.com> έγραψε:

Do you have anything connected to the board?

I had a similar problem and in my case the reason for having the board crashing all the time was a damaged thermistor. It seems like if a sensor (endstops should cause this problem too) is shorted, marlin is prevented from booting and the board somehow kills it's USB connection.

—
You are receiving this because you authored the thread.
Reply to this email directly, view it on GitHub, or unsubscribe.

Closed 2020-01-22.

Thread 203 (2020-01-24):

Troubleshooting MOSFET driven hotend fan

eschmidt12, 2020-01-24:
I'm in the process of upgrading my printer to a dual extruder setup with the TH3D Tough dual hotend, Petsfang mount, and the SKR V1.4 main board running 2209 drivers.

The issue I'm having is that, because I'm now using both HE0 and HE1 outputs for extruders, I don't have a g-code controlled hotend cooling fan. I could run the fan easily enough all the time, but I really want to be able to use the auto fan capability, i.e. only on when the hotend is over 50C.

Here's the configuration I'm trying to troubleshoot now:

* Marlin 2.0.x bugfix
* IRF520 MOSFET module driving the fan:
   * VIN and GND from the PSU
   * V+ and V- connected to the fan
   * SIG and GND connected to the E0DET pins 1.26 and GND. E0DET is typically configured as the filament runout sensor, and is right next to the x, y, and z endstop pins.
* In Configuration\_adv.h:
   * \#define E0\_AUTO\_FAN\_PIN P1\_26
* In Pins\_BTT\_SKR\_V1\_4.h:
   * //#define FIL\_RUNOUT\_PIN     P1\_26
   * \#define FAN1\_PIN          P1\_26
* In Configuration.h:
   * \#define ENDSTOPPULLUPS

Here's the problem:

What I'm finding is that the MOS module is behaving correctly if I drive its SIG pin with a known 3.3/5V source (i.e. the +5V pin on E0DET). The fan runs and everything, no worries. But I can't get the SIG pin on the SKR V1.4 to output a voltage to drive the MOS module.

* If I measure the voltage between +5 and GND at E0DET, I get +5V, as expected
* If I measure the voltage between SIG and GND at E0DET, I get \~20mV when I expect it to be in the "off" state
* If I measure the voltage between SIG and GND at E0DET, I get \~240mV when I expect it to be in the "on" state. I can observe the voltage change occur exactly when the AUTO\_FAN\_PIN configuration should trigger it, when the hotend temperature crosses the 50C threshold.
* If I measure the voltage between the SIG and GND pins for E1DET and PWRDET, I get somewhat random readings. If I measure between SIG and GND for X, Y, and Z-stop pins, I get a solid 3.3V.

So the E0DET pin seems to be changing state as expected, but the "on" voltage of \~240mV is a small fraction of what I expect it to be, therefore it can't trigger the MOSFET.

What am I missing? Do I have a defective board? An incorrect configuration of the firmware? Are those the wrong pins to use? I'd love some help figuring this one out.

OleUrgast, 2020-01-29:
If I remember correctly, all endstop connectors have hardware resistors and capacitators on SKR boards.  You actually send your signal through a voltage devider if using them as output. While this is wanted on input (as I/O of CPU is 3.3 V but input should be 5V (or even 5.5V) tolerant) it also reduce 3.3V to a value to low to switch a mosfet. This a disadvantage in using a 32bit CPU with 3.3V instead 5V 8 bit Arduino...
Depending on your display, some pins on EXP1/2 should be free to use (i.e. if you do not use an 2004 LCD). These have no resistors attached, as they are output anyway (even displays with 5 V accept 3.3V as high) so they should work fine (have not testet myself).

eschmidt12, 2020-01-29:
> If I remember correctly, all endstop connectors have hardware resistors and capacitators on SKR boards. You actually send your signal through a voltage devider if using them as output. While this is wanted on input (as I/O of CPU is 3.3 V but input should be 5V (or even 5.5V) tolerant) it also reduce 3.3V to a value to low to switch a mosfet. This a disadvantage in using a 32bit CPU with 3.3V instead 5V 8 bit Arduino...
> Depending on your display, some pins on EXP1/2 should be free to use (i.e. if you do not use an 2004 LCD). These have no resistors attached, as they are output anyway (even displays with 5 V accept 3.3V as high) so they should work fine (have not testet myself).

Thanks for the feedback. You might be right, but in that case why would I see different behavior between the x, y, and z min connector pins, and the E0DET, E1DET, and PWRDET pins? I get 3.3V to the 3 latter, measured at the pins.

I’m running the stock Ender 5 LCD...any idea if that has available EXP1/2 pins?

OleUrgast, 2020-01-29:
It might be Marlin switching internal pullup/pulldown resistors in addition to the hardware ones...

in https://github.com/bigtreetech/BIGTREETECH-SKR-V1.3/blob/master/BTT%20SKR%20V1.4/Firmware/Marlin-2.0.x-SKR-V1.4-Turbo/Marlin/src/pins/lpc1769/pins_BTT_SKR_V1_4_Turbo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 you find pin definitions used for different displays; beginning in line 178.
Ender 5 uses CR10 display. So if you use only one ribbon cable to exp3 of display, connect it to exp1 on board and activate cr10 display in marlin, the standard definition of exp1 / exp2 is changed by:
```
  #if ENABLED(CR10_STOCKDISPLAY)
    #define LCD_PINS_RS    P1_22
    #define BTN_EN1        P1_18
    #define BTN_EN2        P1_20
    #define LCD_PINS_ENABLE P1_23
    #define LCD_PINS_D4    P1_21
```

Normal setup at EXP1/2 is:
```
 *              _____                                             _____
 *          NC | · · | GND                                    5V | · · | GND
 *       RESET | · · | 1.31(SD_DETECT)             (LCD_D7) 1.23 | · · | 1.22 (LCD_D6)
 *  (MOSI)0.18 | · · | 3.25(BTN_EN2)               (LCD_D5) 1.21 | · · | 1.20 (LCD_D4)
 * (SD_SS)0.16 | · · | 3.26(BTN_EN1)               (LCD_RS) 1.19 | · · | 1.18 (LCD_EN)
 *   (SCK)0.15 | · · | 0.17(MISO)                 (BTN_ENC) 0.28 | · · | 1.30 (BEEPER)
 *              -----                                             -----
 *              EXP2                                              EXP1
```
So if you connect the display by only one ribbon cable and define CR10 stock display in Marlin, EXP2 is completly free. Not shure if 0.15-0.17 is not used internaly otherwise (does not seem so), but 3.25+3.26 should be free in my opinion.

eschmidt12, 2020-02-02:
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

Implemented using 3.25 and 3.26, everything working perfectly. Thanks!

Closed 2020-02-02.

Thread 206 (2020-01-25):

SKR 1.4 Turbo USB Detection

Baconadors, 2020-01-25:
Hi all,

Just getting my SKR 1.4 Turbo wire up and I seem to be having a problem connecting it via USB.
I have changed the jumper over to USB power. I plug in the provided USB cable to the board and then to my computer.

However it will not show up in explorer.

I check the device manager and I can see a "USB Serial Device (COM4) flashing every few seconds.
I know that this is the SKR board as this behavior stops when I unplug it.

What is the issue? See the attached GIF.
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

bartofborg, 2020-01-25:
You need the driver for it, https://github.com/HobbyComponents/CH340-Drivers

Baconadors, 2020-01-25:
Unfortunately, that driver won't install.

https://i.imgur.com/xpB9M7L.gif

bartofborg, 2020-01-25:
if you open the instruction pdf, ther is a link in it to a driver from bigtree there. it is a dropbox address, you'll have to type it in manually but, it worked for me

Baconadors, 2020-01-25:
I disabled signed driver checking and it allowed me to install both the CH340 driver and the lpc176x_usb_driver included in github.

Still have the same issue with it showing. Same behavior as in the original gif.

Baconadors, 2020-01-25:
If I uninstall the driver right before it disappears, when the device reappears it will show "Marlin USB Device"
It this disappears and the cycle in the original gif continues. At this point I have indeed installed the drivers.

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

Baconadors, 2020-01-25:
When I right click the device and choose update, I was able to switch it over to Marlin USB Serial driver.
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

However, original behavior continues.

bartofborg, 2020-01-25:
Good! You ready to go then.Jeff ZackodnikOn Jan. 25, 2020 12:18 p.m., Baconadors <notifications@github.com> wrote:When I right click the device and choose update, I was able to switch it over to Marlin USB Serial driver.

However, original behavior continues.

—You are receiving this because you commented.Reply to this email directly, view it on GitHub, or unsubscribe.

Baconadors, 2020-01-25:
No, I'm not ready to go.

It still doesn't work.

Baconadors, 2020-01-25:
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

bartofborg, 2020-01-25:
Have you connected the USB to your computer and opened pronterface or whatever terminal program your using and tried connecting to the board on the com port the marlin device is?

Get Outlook for Android

On Sat, Jan 25, 2020 at 12:35 PM -0700, "Baconadors" <notifications@github.com> wrote:

No, I'm not ready to go.

It still doesn't work.

—
You are receiving this because you commented.
Reply to this email directly, view it on GitHub, or unsubscribe.

No, I'm not ready to go.

It still doesn't work.

--
You are receiving this because you commented.
Reply to this email directly or view it on GitHub:
https://github.com/bigtreetech/BIGTREETECH-SKR-V1.3/issues/206#issuecomment-578436223

Baconadors, 2020-01-26:
Wiring issue.

Couldn't directly see what was causing a problem, but I redid all of the wiring and made sure to put electrical tape on anything that could short the board.

PapiOrso, 2020-02-10:
I solved the problem by reloading the original firmware provided in the micro SD. I used a usb card reader to rename the original file from .CUR to .BIN then I inserted the SD in the board.

saintofinternet, 2021-01-19:
> I solved the problem by reloading the original firmware provided in the micro SD. I used a usb card reader to rename the original file from .CUR to .BIN then I inserted the SD in the board.

Does that orginal firmware work for CoreXY?

lakeland3516, 2021-03-02:
the reason the inf file wont' work for people using windows 10 or other windows i found that the 64 bit machines won't recognize the file but if you have a old 32 bit computer kicking around it'll load properly and recognize it so basically saying some one needs to write one for a 64 bit system

Closed 2020-01-26.

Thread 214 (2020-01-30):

SKR 1.4 Turbo | Blank LCD

77katz77, 2020-01-30:
I just finished configuring my BigTreeTech SKR 1.4 Turbo using the provided modifications and configured Marlin 2.0 config.[https://www.dropbox.com/s/ppjfflhf3j5yzh2/MarlinV2.0%20SKRV1.1%20instruction.docx?dl=0](url)
I was able to load the compiled .bin file to the SKR through the SD Card. However, whenever I power the board on, the LCD screen remains blank (but lit). I know the screen works and I don't think anything was modified in the config that would effect the display. I've also tried powering off of the usb and 12v power supply, both result in the same problem. If anyone has any idea what the issue is please let me know.

(Config and Platformio files)
https://github.com/77katz77/SKR1.4-Turbo.git

Cerv4ntez, 2020-01-30:
in your config you defined a #define REPRAP_DISCOUNT_FULL_GRAPHIC_SMART_CONTROLLER

ist that also what you are really using?

77katz77, 2020-01-31:
> in your config you defined a #define REPRAP_DISCOUNT_FULL_GRAPHIC_SMART_CONTROLLER
>
> ist that also what you are really using?

So I was able to define ZONESTAR_LCD (what's used on the anet a8). The problem is now I get an error "'ACD_KEYPAD_PIN' was not declared in this scope" (in temperature.cpp) whenever I try and compile. From what I understand this has to do with how the buttons on the display are assigned. I've seen multiple threads saying to reassign some of the UI_DISPLAY pins. If this is the case how would I achieve this (nothing in Config.h and there doesn't seem to be a Display.h file as others have suggested)?

Cerv4ntez, 2020-01-31:
i would start from example config files for your printer and modify anything concerning the new board much easier than the other way around.

ellensp, 2020-02-01:
Its ADC_KEYPAD_PIN not ACD_KEYPAD_PIN
If just plugged in would go to pin 1.20 but 1.20 is not analog. So this will not work
You would need a special cable to put the analog wire on a unused analog input.
You also have to make sure not to exceed 3.3v, as analog pins are not 5v tolerant.
only these pins are defined as analog...
#define P0_02_A7 P0_02
#define P0_03_A6 P0_03
#define P0_23_A0 P0_23
#define P0_24_A1 P0_24
#define P0_25_A2 P0_25
#define P0_26_A3 P0_26
#define P1_30_A4 P1_30
#define P1_31_A5 P1_31

Your original 12864 screen probably has its cables rotated 180 degrees from the skr1.4. this is very  common , depends on where the screen came from..   I pull off the plastic kyeds sockets on the back of the lcd and plug the cables in backwards, that way they are correct on the controller end.

77katz77, 2020-02-04:
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

Thanks for this detailed explanation. I decided to just buy a TFT 3.5 which I was able to get working pretty easily. If I get the time I'll make sure to come back and hopefully will be able to get the zonestar working.

Closed 2020-02-04.

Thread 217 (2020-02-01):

no BTT SKR V1.4 schematic

ellensp, 2020-02-01:
I wanted to check the endstops pullup resistor values, but no schematics

Please upload schematics

Marsman1970, 2020-02-03:
I would say it would be have the same resistors as the Skr v1.3 they are 10k. If you look at the end-stop connectors on the left there is a row  of resistors going down if there are resistors that say 103 they are 10k. I tried to look at the picture of the 1.4 board but it's not clear enough for me to see. Are you having problems with your end-stops.
Michael

ellensp, 2020-02-03:
You would be wrong... mini ir probes don't work on skr 1.4 endstop pins and they do work on skr 1.3 endstop pins and we know its a different pullup on the board. Just wanted to confirm what value.

Marsman1970, 2020-02-03:
Now you got me interested i had a look at Skr v1.1 and v1.3  and i found that the   v1.1 the limit switch socket and  resistor is connected to 3.3 volt rail and used a 4.7k pull-up resistor but on the v1.3 the limit switch socket   is connected to 5 volt rail and used a 10k pull-up that is connected to the 3.3 volt rail. I wonder what the changed on the 1.4  according to the diagram  the limit switch socket  is still  connected to 5 volt rail i can almost see the a 10k resistor but the image is just not clear enough.
Michael

DeviousPenguin, 2020-02-06:
Schematics or even the components used would be good to have.

I'd quite like to safely run my motors at a higher voltage than 24v, but with no schematics or component list I have no idea how safe this is!

rrichX, 2020-02-09:
I raised a question over end stop behaviour last week in the Marlin Support Discord channel.

I went from a SKR 1.3 > 1.4 and my IR Probe failed to work - being reported as Trigger, reading around I decided to give the probe pin a try and now it works - doing an M48 it's far more accurate than it ever was on the 1.3.

I did break out my magnifier and as far as I can, the values have changed of the resistors but I'm also curious to why the probe pin works so much better. I thought I had read about changes to the end stops to help optical end stops, I wonder if my issue is a result of changes.

asdmin, 2020-03-09:
dup to https://github.com/bigtreetech/BIGTREETECH-SKR-V1.3/issues/184

Closed 2020-03-10.

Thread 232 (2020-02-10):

SKR1.4 and BLTouch Probe

superperf, 2020-02-10:
Hi Guys,

i received my new SKR1.4 Board and tried to swap it agains my defective SKR1.3. I Tried :D.

Everything is working now, but i wanted to mention an Issue i ran into with the BLTouch and the new PIN Header for it.

It seems that the Configuration on this Board for the BLTouch is much different than the other boards (where the probe is plugged in in the Z-Min Header).

I had 2 different Approaches to get this thing to work without Luck:

First: Use the BLtouch Header and configure it like on the SKR1.3 Board with
**_#define Z_MIN_PROBE_USES_Z_MIN_ENDSTOP_PIN_** enabled

My Problem:
The Bltouch Starting as expected and deploys its pin, but quickly stows after this and the Z-Axis isnt moving towards the Nozzle.
M119 gives a Triggered State for Z-Min

Second: Tried to declare the P0_10 pin in
**_#define Z_MIN_PROBE_PIN P0_10_**

Problem: The Bltouch wont get an Signal to deploy its Pin but the Z-Axis is still moving to Nozzle cause the Z-Probe-endstop is showing "open"

So I Think there is some Software Issue in Combination with the dedicated BLTouch Z-Min Header.

My Workaround Solution for now, which is working well is:

Set everything normal like in the Manuals listed for BLTouch. BUT change one Line in the pins_BTT_SKR_V1_4.h file.

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

just change the Z_STOP_PIN to P0_10 (the bltouch pin header)

This is because in the File pins.h the Z_MIN_PIN is declared as Z_STOP_PIN

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

Thats why in my First attempt the Z-Min Endstop was triggered and not Open when the BLTouch tried to Level. Cause the Z-Min endstop was unassigned.

I Hope Someone will step over this Issue. Maybe there is someone who's got a nicer Workaround. At Least my BLTouch is working again and my Printer is ready to Print :)

stantond, 2020-02-11:
Search the issues in this repo, there's already an issue here with a solution

lijinlin19970813, 2020-02-18:
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

I think you should disable Z_MIN_PROBE_USES_Z_MIN_ENDSTOP_PIN in the configuration.h file (the default is on), and then use the default bltouch pin in the pin file.

thisismike97, 2020-02-24:
@superperf If you are still having issues with your bltouch take a look at my config, i got it all working recently. (SKR 1.4 turbo and bltouch smart v3.1)

**Remember to close this issue if your problem has been resolved.**

cronos45, 2020-03-12:
@thisismike97 Where may I find said config sir?

thisismike97, 2020-03-12:
@cronos45 My marlin fork on github has my configs.

Closed 2020-03-12.

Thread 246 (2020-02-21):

accidental short circuit, any chance of repair?

MikRoscope, 2020-02-21:
I accidentally shorted the 12/24V and GND pins on top left (near X axis motor connector) of my BTT SKR V1.3 while the board was on 24V power.. after a spark the board seems to be dead. Is there any chance a voltage regulator is burned and could be replaced? or the processor is dead? I could not find the schematics to follow the connections to that pin.

Andy-ABTec, 2020-02-22:
Hi, schematic is [HERE](https://github.com/bigtreetech/BIGTREETECH-SKR-V1.3/blob/master/BTT%20SKR%20V1.3/hardware/SKR-V1.3-SCH.pdf) - good luck...

MikRoscope, 2020-02-22:
thanks for the link, I had a look, but not sure which part of schematics is the pin I shorted.. is that the pin connected directly to VBB in bottom left of the schematics?
otherwise when I power the board now the red led on bottom left is lighted but very dim, and the chip marked here gets hot very fast
https://imgur.com/a/4XWL4eF

thisismike97, 2020-02-24:
The chip you marked probably has a short around it somewhere, check around with a multimeter.

You'll probably have to replace that chip and maybe even more, fixing that chip could reveal the next problem and so on..

Considering the time investment and finding the correct replacement parts its probably better to just get a new board.

MikRoscope, 2020-02-24:
Thanks a lot for the tip! I will check that chip and around it. I have access to few replacement parts.
I have already ordered a new board, until the new board arrives, I like to try to fix this one as a hobby before throwing it out! ;)

thisismike97, 2020-02-24:
@MikRoscope I also recommend testing the board using only usb power instead of your 12/24v power supply, a lot of the parts can handle the 5v usb but would die instantly on 12 volt or higher while there are still short circuits present.

If you manage to fix it, you could always return the new board, you got nothing to loose, goodluck!

Also don't forget to close this issue after the repairs / new board.

MikRoscope, 2020-02-24:
@thisismike97 That is a good idea, I will work on USB power to check the board.

After close inspection of the area near U4 (the chip that gets hot fast) I noticed clear burn marks on LV5, C12 and LV4 as seen the image below. LV4 and LV5 are 22microH inductors and C12 is 0.1microF capacitor based on the schematics. I am not sure about their correct smd size or rating though. If I could find them in my local electronic shop, I will replace them first.

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

thisismike97, 2020-02-24:
@MikRoscope yup, i also checked the schematic just now, those burned components are part of the 3.3v rail, however maybe those components blowing up saved your SOC. though at this point i highly suspect it's beyond repair.

I'm pretty curious, let me know if you succeed.

MikRoscope, 2020-02-25:
I replaced the broken components but still U4 as well as the SOC gets very hot even on 5V usb! Unfortunately, the board is beyond repair for me!

Closed 2020-02-25.

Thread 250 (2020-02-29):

Skr 1.4 Turbo TMC 2209 v2 Watterott:TMC Connection Error

schuuuu, 2020-02-29:
Trying to setup tmc 2209 v2 from watterott with a skr 1.4 turbo. Followed the instructions on learn.watterott and cut off the spread pin +soldering bridge on skr + jumper is set. Used latest marlin Bugfix and also bigtreech version, but still getting TMC Connection error. Motors can be moved.

Any suggestions to fix the issue?

TobiasFechner, 2020-02-29:
I had the same problem. Here is the solution:

You have to make a solder bridge on the underside of each TMC2209 stepper board to get the Uart signal in/ out using one of the PDN_UART pins. If you turn the board around you can see three little solder pads. If you look at the bottom side of the stepper board with the three diag pin holes oriented to to the left, just connect the middle pad with the left pad. That should do the trick.

Also the communication to the driver will only work if a power supply is connected (e.g. 12V or 24V).

Regards
Tobi

schuuuu, 2020-02-29:
Thanks Tobi. Tested it and it works fine.

Best regards

Marvin

kevinmorrison, 2020-04-21:
Having this issue but not sure what three pads you are talking about? I see a couple of places that have three pads and dont want to solder the wrong ones. Any better clue where these are?

schuuuu, 2020-04-22:
Hey Kevin,

do you have TMC 2209 from Watterott and SKR 1.4 Turbo? If so just upload a picture of your stepper driver.

Best regards

Marvin

kevinmorrison, 2020-04-22:
Thanks Marvin, I was going to just delete this post because I discovered the problem and I am a bit embarrassed. What I figured out is the risers that the pins on the driver go into on the MB are weak and when I was pushing them onto the MB the riser was bent out just far enough that the pins slid down the inside of the riser instead of going into the holes intended for them. So of course no connection was being made. I find these types of high risers to be problematic in that they apparently can be loose from the factory. There has got to be a better way to mount these than going with these high flying connections that have weak joint to the MB. Anyway that is what happened to me and hopefully someone else having issues will read this and find the same thing was happening to them.

Closed 2020-02-29.

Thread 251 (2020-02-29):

Skr 1.4 Turbo TMC 2209 v1.2 - Two Z steppers dont work

ROMSY, 2020-02-29:
i am replacing my board right now and trying to get my two z-steppers on one driver to work.
x and y just work fine, and also my first test with one stepper on z.
but when i put a second stepper on z its like he has not enought power (motor does only make a weird sound) what could be the problem here?

JRosello, 2020-02-29:
Interested on this issue... I'm just waiting to arrive my board to fit in my cr10s that has 2 Z steppers.

paulgking, 2020-03-01:
You might want to give a bit more detail. I'm using a 1.4 (no turbo) with TMC2209 and no problems dual z axis now.

So what stepper driver are you using etc. ? Not that it'll guarantee help, but at the moment you are asking people to work blind to your setup other than the board.

ROMSY, 2020-03-02:
Hey,
sorry i am very new with the 3d Printer stuff (and changing the board) The printer is an FLSUN Cube and the Stepper Motors i am using are: SL 42STH40-1504A
Unfortunatally its the info on the left motor, on the right motor there is no info at all. but after checking x and y there is also no info on on of the steppers and the second on has the same info so i guess those are all the same steppers?

So far i changed to voltage in configuration_adv from 800 to 1100 and it started to work but now those two are really noisy.
i left mostly every value on its default settings but changed  DEFAULT_AXIS_STEPS_PER_UNIT  on x and y to 160, 160 (z has still the default of 4000 maybe i should double it too?)

since it makes a heavy noise i gonna check out later when i am back from work if its a mechanical issue with the sound.

is there more information i can /should provide?

ROMSY, 2020-03-02:
Update:
i turn on the printer and move Z... its super noisy!
i start pronterface and put in **M92 Z4000** and THEN move z, its silent as the other motors.
Question is now what could case this behaviour?

paulgking, 2020-03-03:
The times I have had very noisy Z was either mechanical where thing were too tight, or the motor current was too high. Did you increase the current pot on the motor driver when trying other things?

ROMSY, 2020-03-03:
Ok, i am sorry: i downloaded the latest version from the marlin website instead the one from github.
after reflashing this one everything works out of the box. so i just need to update the 2.0.1 to 2.0.4.4 it was all my fault ><

Closed 2020-03-03.

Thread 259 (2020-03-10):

SKR 1.4 turbo BTT with TMC2209 BTT V1.2 E0 direction

onebehler, 2020-03-10:
I am having a problem with two seperate BTT SKR 1.4 Turbo paired with BTT TMC2209 V1.2 drivers moving the extruder in both directions.  I can send the g1 e10 and g1 e-10 and the motor spins in the same direction.

I have removed the cold extruder block from my firmware, tried several different motors with different cabling, swapped drivers from one that works in both directions.  I set the lone jumper per driver slot for UART mode as described in the manual. I am using sensorless homing and bltouch.  I have looked at several different web sources to find where my error is.  I cloned the github last week and am working with VS and PIO to compile and make.  Any help is greatly appreciated.

[Config.zip](https://github.com/bigtreetech/BIGTREETECH-SKR-V1.3/files/4315338/Config.zip)

onebehler, 2020-03-11:
Found the problem. I changed #define SERIAL_PORT away from 0 to 2 and that caused my loss of bi-directional control. Thank you so very much for @ellensp over at the Marlin github for help on this. I might never have gotten this figured out.  I will mark closed.

Closed 2020-03-11.

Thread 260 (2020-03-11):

SKR 1.3 + TMC5160 CNC FAN always works

superkefir, 2020-03-11:
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
Hello,i have one problem. I install SKR 1.3 + TMC5160 v1.2 instead of MKS_GEN_L+2100
But after configuration files when i turn on the printer it always burn LED signal near the CNC FAN out and always works fan of the layer.
So when i connect it to my PC and send M107 or M106 S0 nothing changes. From TFT the same one.
I thought that it is the problem of binding P2_03, so i add #define FAN_PIN to pins_BTT_SKR_V1_3.h but it deosn\t help. After glashing firmware the fan starts always. How can i make it works properly?

[Marlin.zip](https://github.com/bigtreetech/BIGTREETECH-SKR-V1.3/files/4319149/Marlin.zip)

superkefir, 2020-03-12:
Little update. I change tha motherboard to new one to test if the problem in mosfet.
So the situation is the same. When the DC24V fan connected it is turned off, when it's disconnected the led is turning off. I take multimeter to check voltage and change power of this pin. It was changed succesfully from 0V to 24V. So i thought there is a problem in a fan. I take another one 24V and connect it. It starts too too full power with power off to this pin. What i make wrong? I checked two 5015(24V) fans, one 4020, and two new 5015 (24v) from the box. So the situation is the same. I connect it to the motherboard without and cable. So the pin works and shows voltage only until i connect the fan to this pin.

superkefir, 2020-03-12:
Problem found! The screw for mount adapter make short circuit between the FAN pins when FAN was connected.

Closed 2020-03-12.

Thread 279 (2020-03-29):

No output on Hot Bed - very low output voltage

Gavin152, 2020-03-29:
So, I finally got around to swapping the stock melzi board of my CR10 for an SKR 1.4 and everything went pretty smoothly so far. However, somehow I can't get the heated bed to work.

The Cr10 is using an external Mosfet and I was panning on continuing to use it. So I'm wiring the bed output on the SKR to the control input of the Mosfet. I'm getting "Heating failed" errors everytime I try to heat the bed. I've narrowed it down so far as I can tell, that the hot bed output on the board is not turning on. I measured the voltage on the board and I only get around 400 mV on the hot bed output (when I turn the bed on) and also the LED next to the Q2 Mosfet is not lighting up.

Could I be simply dealing with a faulty board or is something in my marlin configuration messed up (this is my first time setting up marlin): https://github.com/Gavin152/cr10marlinconf/blob/master/Configuration.h.

Any hints would be greatly appreciated.

Talha909, 2020-04-22:
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

Did you find any solution. I have the same issue.

Gavin152, 2020-04-22:
> Did you find any solution. I have the same issue.

Yes, damn, meant to post this here anyway.

I ended up setting the hotend2 output as the bed output. From there I'm using the external MOSFET of the CR10. As long as there's a separate MOSFET in use, there won't be too much current pulled from the output on the board.

Hope this makes sense.

quaint-engineer, 2020-08-10:
This just happened to my SKR 1.4 on my Sidewinder X1. One of my Z steppers started to make a clicking noise also while plugged into E1 also.

gustavomiguelsa, 2021-04-10:
Definitely late to this but did you connect the 'Bed Power In' terminals to your PSU, in addition to connecting the MOSFET signal wire to the 'Hot Bed Out' terminals? Without current flowing to those 'Bed Power In' there's no way the MOSFET signal wire is gonna pass it through to the MOSFET
Leaving this here as future reference for GTR v1.0 or SKR Pro users

jakebullet70, 2024-04-14:
> This just happened to my SKR 1.4 on my Sidewinder X1. One of my Z steppers started to make a clicking noise also while plugged into E1

WOW, Same clicking sound and now dead bed on E1. How did you fix it?

Closed 2020-04-22.

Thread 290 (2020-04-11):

TMC5160 SKR 1.3->1.4 turbo : Testing X connection ALL HIGH

superkefir, 2020-04-11:
Hello, i have a problem with my new 5160 v1.2 drivers.
I got three boards: 2 pcs SKR 1.3 and one SKR 1.4 Turbo.
I have Marlin 2.0.5.2 - > 2.0.5.3 versions
When i turn off the board and send M122 i see:
ПОЛУЧЕНО: Driver registers:
ПОЛУЧЕНО: 		X	0x80:06:40:00
ПОЛУЧЕНО: 		Y	0x80:07:40:00
ПОЛУЧЕНО: 		Z	0x80:04:40:00
ПОЛУЧЕНО: 		Z2	0x80:04:40:00
ПОЛУЧЕНО: 		E	0x80:04:40:00
Testing X (and all others) connection... OK

Also i can see M913 result of threshold.

But when i start the print during the start g-code i send M122 and i the result is always: Testing X connection ALL HIGH on all drivers. When i stop the print it's the same. Untill i reboot the board. Then everything goes in a circle.

Is it wrong connection of wires or smth else?
I can't find the solution to this problem for three days by google, so maybe you can help me.

superkefir, 2020-04-11:
Little update.
I check diag pin and turn it off, i turn off sensorless homing.
Then i checked G-code after what line it's bugged.
So if i turn printer then send M122 it's ok and shows registers and connection ok.
Then i send M109 S220 T0
And printer echo busy. At this moment i send M122.
And right after busy lines when the temperature get's stabilized i get the error by all drivers and no connection.

Mace-maker, 2020-06-06:
I have the same problem 1.4t did you find a solution?

superkefir, 2020-06-06:
Yes i unbind the pins. TMC_SW_SCK and RGB_LED_G_PIN had the same pin so after starting the print the pin of led blocked the pin of TMC_SW_SCK. So i have to unbind it.
This one:
  #define RGB_LED_G_PIN 4

Mace-maker, 2020-06-06:
Ok, thx, I don’t think I have led uncommented, but I’ll check it tomorrow. Pins file and Configuration.h?

superkefir, 2020-06-07:
Yes, also you can check M43 output to find if there any pins are double used.

Mace-maker, 2020-06-07:
I don’t know exactly what I’m looking for, but I can’t see pin numbers that are assigned to two variables at the same time, maybe the empty “.”s without numbers like E1_DIAG_PIN mean that they’re not set properly? Only diag I can see are on the drivers themselves?
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

superkefir, 2020-06-08:
You can compare with my output log.
ПОЛУЧЕНО: PIN: 0.00        <unused/unknown>                       Input  = 1               
ПОЛУЧЕНО: PIN: 0.01        <unused/unknown>                       Input  = 1               
ПОЛУЧЕНО: PIN: 0.02 (A 2)  TXD0                                   Input  = 1
ПОЛУЧЕНО: PIN: 0.03 (A 3)  RXD0                                   Input  = 1
ПОЛУЧЕНО: PIN: 0.04        TMC_SW_SCK                             Output = 1
ПОЛУЧЕНО: PIN: 0.05        TMC_SW_MISO                            Input  = 1
ПОЛУЧЕНО: PIN: 0.06        <unused/unknown>                       Output = 1               
ПОЛУЧЕНО: PIN: 0.07        <unused/unknown>                       Input  = 0               
ПОЛУЧЕНО: PIN: 0.08        <unused/unknown>                       Input  = 1               
ПОЛУЧЕНО: PIN: 0.09        <unused/unknown>                       Input  = 1               
ПОЛУЧЕНО: PIN: 0.10        <unused/unknown>                       Input  = 1               
ПОЛУЧЕНО: PIN: 0.11        E0_DIR_PIN                             protected
ПОЛУЧЕНО: PIN: 0.15        SCK_PIN                                Input  = 1
ПОЛУЧЕНО: PIN: 0.16        SDSS                                   Analog in =     0
ПОЛУЧЕНО: .                SS_PIN                                 Output = 1
ПОЛУЧЕНО: PIN: 0.17        MISO_PIN                               Input  = 1
ПОЛУЧЕНО: PIN: 0.18        MOSI_PIN                               Input  = 1
ПОЛУЧЕНО: PIN: 0.19        Y_STEP_PIN                             protected
ПОЛУЧЕНО: PIN: 0.20        Y_DIR_PIN                              protected
ПОЛУЧЕНО: PIN: 0.21        Z_ENABLE_PIN                           protected
ПОЛУЧЕНО: PIN: 0.22        Z_STEP_PIN                             protected
ПОЛУЧЕНО: PIN: 0.23 (A23)  <unused/unknown>   Analog in =     0   Input  = 0               
ПОЛУЧЕНО: PIN: 0.24 (A24)  <unused/unknown>   Analog in =   975   Input  = 0               
ПОЛУЧЕНО: PIN: 0.25 (A25)  <unused/unknown>   Analog in =   974   Input  = 0               
ПОЛУЧЕНО: PIN: 0.26 (A26)  <unused/unknown>   Analog in =   823   Input  = 0               
ПОЛУЧЕНО: PIN: 0.27        <unused/unknown>                       Input  = 0               
ПОЛУЧЕНО: PIN: 0.28        <unused/unknown>                       Input  = 1               
ПОЛУЧЕНО: PIN: 0.29        <unused/unknown>                       Input  = 1               
ПОЛУЧЕНО: PIN: 0.30        <unused/unknown>                       Input  = 0               
ПОЛУЧЕНО: PIN: 1.00        POWER_LOSS_PIN                         Input  = 1
ПОЛУЧЕНО: PIN: 1.01        E1_CS_PIN                              protected
ПОЛУЧЕНО: .                Z2_CS_PIN                              protected
ПОЛУЧЕНО: PIN: 1.04        E0_CS_PIN                              protected
ПОЛУЧЕНО: PIN: 1.08        Z_CS_PIN                               protected
ПОЛУЧЕНО: PIN: 1.09        Y_CS_PIN                               protected
ПОЛУЧЕНО: PIN: 1.10        X_CS_PIN                               protected
ПОЛУЧЕНО: PIN: 1.14        E1_DIR_PIN                             protected
ПОЛУЧЕНО: .                Z2_DIR_PIN                             protected
ПОЛУЧЕНО: PIN: 1.15        E1_STEP_PIN                            protected
ПОЛУЧЕНО: .                Z2_STEP_PIN                            protected
ПОЛУЧЕНО: PIN: 1.16        E1_ENABLE_PIN                          protected
ПОЛУЧЕНО: .                Z2_ENABLE_PIN                          protected
ПОЛУЧЕНО: PIN: 1.17        TMC_SW_MOSI                            Output = 0
ПОЛУЧЕНО: PIN: 1.18        <unused/unknown>                       Output = 1               
ПОЛУЧЕНО: PIN: 1.19        <unused/unknown>                       Output = 1               
ПОЛУЧЕНО: PIN: 1.20        <unused/unknown>                       Output = 1               
ПОЛУЧЕНО: PIN: 1.21        <unused/unknown>                       Output = 1               
ПОЛУЧЕНО: PIN: 1.22        <unused/unknown>                       Input  = 1               
ПОЛУЧЕНО: PIN: 1.23        <unused/unknown>                       Input  = 1               
ПОЛУЧЕНО: PIN: 1.24        NEOPIXEL_PIN                           Input  = 0
ПОЛУЧЕНО: PIN: 1.25        FIL_RUNOUT2_PIN                        Input  = 1
ПОЛУЧЕНО: .                E1_DIAG_PIN                            Input  = 1
ПОЛУЧЕНО: PIN: 1.26        E0_DIAG_PIN                            Input  = 1
ПОЛУЧЕНО: PIN: 1.27        Z_MIN_PIN                              protected
ПОЛУЧЕНО: .                Z_DIAG_PIN                             protected
ПОЛУЧЕНО: .                Z_STOP_PIN                             protected
ПОЛУЧЕНО: PIN: 1.28        Y_MIN_PIN                              protected
ПОЛУЧЕНО: .                Y_DIAG_PIN                             protected
ПОЛУЧЕНО: .                Y_STOP_PIN                             protected
ПОЛУЧЕНО: PIN: 1.29        X_MIN_PIN                              protected
ПОЛУЧЕНО: .                X_DIAG_PIN                             protected
ПОЛУЧЕНО: .                X_STOP_PIN                             protected
ПОЛУЧЕНО: PIN: 1.30 (A62)  <unused/unknown>   Analog in =   757   Input  = 0               
ПОЛУЧЕНО: PIN: 1.31 (A63)  <unused/unknown>   Analog in =   741   Input  = 0               
ПОЛУЧЕНО: PIN: 2.00        SERVO0_PIN                             Analog in =     0
ПОЛУЧЕНО: PIN: 2.01        X_ENABLE_PIN                           protected
ПОЛУЧЕНО: PIN: 2.02        X_STEP_PIN                             protected
ПОЛУЧЕНО: PIN: 2.03        FAN_PIN                                protected
ПОЛУЧЕНО: PIN: 2.04        E0_AUTO_FAN_PIN                        protected
ПОЛУЧЕНО: .                FAN1_PIN                               protected
ПОЛУЧЕНО: PIN: 2.05        HEATER_BED_PIN                         protected
ПОЛУЧЕНО: PIN: 2.06        X_DIR_PIN                              protected
ПОЛУЧЕНО: PIN: 2.07        HEATER_0_PIN                           protected
ПОЛУЧЕНО: PIN: 2.08        Y_ENABLE_PIN                           protected
ПОЛУЧЕНО: PIN: 2.09        <unused/unknown>                       Input  = 0               
ПОЛУЧЕНО: PIN: 2.10        <unused/unknown>                       Input  = 1               
ПОЛУЧЕНО: PIN: 2.11        Z_DIR_PIN                              protected
ПОЛУЧЕНО: PIN: 2.12        E0_ENABLE_PIN                          protected
ПОЛУЧЕНО: PIN: 2.13        E0_STEP_PIN                            protected
ПОЛУЧЕНО: PIN: 3.25        <unused/unknown>                       Input  = 1               
ПОЛУЧЕНО: PIN: 3.26        <unused/unknown>                       Input  = 1               
ПОЛУЧЕНО: PIN: 4.28        <unused/unknown>                       Input  = 1               
ПОЛУЧЕНО: PIN: 4.29        <unused/unknown>                       Input  = 1               

It seems like some pins are used twice. What configuration you use for your printer?

Mace-maker, 2020-06-08:
Yeah, looks like where I have empty points that might mean double use like filament run out, I’m using kay3d cheetah 5.0 firmware, I have a bl touch and filament run out sensor. Parallel lead screws so 2 Zs,  nothing special.
The TFT 35 is working, but I see points there too.
Thanks for the file, I’ll investigate end of the week after work.

Closed 2020-04-15.

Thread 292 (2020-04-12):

TFT 24 V1.1 not connecting to SKR V 1.4 Turbo

j3cc, 2020-04-12:
I do not get a working connection to my tft 24 V1.1. I successfully updated the firmware of both parts. I flashed the tft from firmware version 1.23 to the latest (1.26) which I downloaded as binary and put on the sd-card. Update was successful.
I also compiled the latest marlin 2.0 with platform.io and successfully loaded it onto the SKR 1.4 Turbo board. I can see an external drive with the firmware on, if I plug the motherboard in. With pronterface however, I can't get a connection running. It correctly recognizes the external device, but no matter what baud raute i put in, no connection to printer this way possible.

The tft24 does also not connect to the skr 1.4 turbo board. It just says "No printer attached". No matter what I enter as connection rate, it does not work.
I already plugged out the thermistors of the printer because I've read that there may be some problems with them but to no avail.
How do I go about debugging this issue? Are there some light blinking codes or something that indicate the skr 1.4 turbo is working as intended?

I am using TMC2209 steppers and set them up in UART mode with jumper positioning as described in the manual

Thx in advance

j3cc, 2020-04-12:
Ok, I finally figured it out. The screen has to be connected via RS232 interface. If it is only connected via EXP1 and EXP2, it will not connect to the board.

RavenDwn, 2020-06-17:
I have the same issue hooked up on rs232 but still can not get it to attach printer. I thought there was a post or video to change config but can't find it.
Any thought on how the get it to read board? All firmware has been updated with success except printer

Closed 2020-04-12.

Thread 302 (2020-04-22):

Suddenly boots up with MAXTEMP HEATBED and no USB connection

bywebberen, 2020-04-22:
This is soooo alarming, I have been printing for months with this board on my DADSON PRUSA i3 - Today I turned it on on the speaker started beeping with the error "maxtemp error" heatbed.

 Then I thought - I'll just reflash the marlin (since it has been working fine) -only to find that there is not a USB connection anymore when i connect to my computer. HMMMM... Okay so I pull the sd card and put the firmware directly to the sd card from platform.io - reinserted and did a reset (like always) still error persists, and no USB still. But if i take the SD-card out it will show that the firmware was indeed updated.  . .

WTF??

Alarming because I actually ordered a bunch og these SKR v1.3 cards to upgrade my other printers.

bywebberen, 2020-04-22:
UPDATE:
If I disable the "heatbed" in marlin sensor statement 0 instead of 1 it will power on and print. And the USB connection works again...

Marsman1970, 2020-04-23:
Can you check the sensor Maybe you have broken wires to the sensor.
Michael

bywebberen, 2020-04-23:
I did that already, I replaced it with a new one, same result... 🤔

Venlig hilsen / best regards
Niels Østbjerg
Syrenvænget 8
5792 Årslev

+45 40630201

tor. 23. apr. 2020 10.00 skrev Marsman1970 <notifications@github.com>:

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

bywebberen, 2020-04-23:
Also if I set the sensor to 0 in marlin, the printer will run, the USB will
work, but of course with no heated bed..

Venlig hilsen / best regards
Niels Østbjerg
Syrenvænget 8
5792 Årslev

+45 40630201

tor. 23. apr. 2020 14.48 skrev Niels Østbjerg <webberen2502@gmail.com>:

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

bywebberen, 2020-04-25:
Okay, so this time I fired it up, now it does not work at all! 12v goes to the fan through the board, but nothing else works...

Crap!

bywebberen, 2020-04-25:
flashed my marlin compile to another SKR v1.3 board - it works - too bad the faulted board only worked a couple of months, that could end up being expensive...

I would love to hear some ideas how to trobleshoot it - and fix it ...

bywebberen, 2020-04-26:
all of a sudden the new SKR v1.3 board dropped the heatbed saying -14 degrees C and starts beeping away???

I have only tested and made firmware changes ?

Any ideas ?

bywebberen, 2020-04-26:
> Can you check the sensor Maybe you have broken wires to the sensor.
> Michael

Still the sensor is fine...

bywebberen, 2020-04-26:
And with this reset... now it suddenly jumped to 16 degrees, while the hotend stays at roomtemp 23

bywebberen, 2020-04-26:
Might have been a broken wire after all...

Marsman1970, 2020-04-27:
Good to hear you sorted it.

Closed 2020-04-26.

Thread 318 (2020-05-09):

HE1 as HE Fan not staying on causing plastic blockage inside HE

ngathant, 2020-05-09:
Hi all, I'm looking for advice on how to get HE fan to work properly on SKR v1.4 Turbo. I've read most of the reddit, git hub posts I could find. I'm running the latest Marlin 2.0.x. The fan is supposed to turn on automatically past 50'C but it's not running most of the time. During a print it comes on briefly about 3 seconds only. So all that melted plastic end up blocking my HE. Here's where I'm at.

I wired it to HE1 port on the turbo and in conguration_adv.h, I set
#define E0_AUTO_FAN_PIN P2_04 & #define EXTRUDER_AUTO_FAN_TEMPERATURE 50.
No dice.

I also tried it as #define E0_AUTO_FAN_PIN FAN1_PIN and made sure FAN1_PIN is P2_04 in pins_BTT_SKR_common.h file. There's a bug in Marlin 2.0.x as the _common file has a variable called HOTENDS which should be EXTRUDERS as in the configuration.h file but if I set E0_AUTO_FAN_PIN as P2_04, that shouldn't really matter.  The CNC FAN0 is working without any issues. I wished BTT has set FAN1 as CNC as well. Any idea why HE1 isn't staying on even past 50'C?

ngathant, 2020-05-09:
The issue was with Creality wiring. They decided to switch yellow and white cables from one end to black and red cables at the other and vice versa at the radial power connector for the hot end. After swapping them out, #define E0_AUTO_FAN_PIN P2_04 & #define EXTRUDER_AUTO_FAN_TEMPERATURE 50 is running the HE fan.

Closed 2020-05-09.

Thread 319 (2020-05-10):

No USB connection on Marlin but I do with Smoothie

ped7284, 2020-05-10:
This is a self created issue.  This is a DIY printer with TFT35, SKR 1.3 TMC2208
I keep adding things to the SKR 1.3 till it breaks.  different extruder, moving limits sensors.  I think I tightened the hotend and since it is a volcano the heat element gets very close to the cool part.  That is the last thing I did that could cause an electrical short. All other connections are tight and the printer has been working great!  I am using VS studio platformIO Marlin bugfix 2.0

History: I noticed the hotend was on after power up. touched it and burnt my finger.   I reset and the the same issue.  cycle power and same thing. I hooked up to the PC and USB drive showed gibberish characters and it looked like corrupted files.  So then I formatted SDcard while it was in the SKR and that was the last of it. after that the USB would not show up on the PC.  I took out the SD card, placed in PC and it worked so I formatted the SD card again and installed the firmware.bin. put back in the SKR and no communications to TFT and hotend still on.  I took out the SD card and it showed firmware.cur so it took but still no USB drive and no TFT connection.

Tried other SD card, different power supply, int vs external pin, disconnected everything and still nothing.   I ended up buying a new board.

BUT then I installed a firmware.BIN from a smoothie location and now the SKR shows the USB connection on the PC and it works with various Mcode commands. https://github.com/bigtreetech/Smoothieware/tree/edge/FirmwareBin

So for a $20 board I have already spent the money typing but I thought this was weird and wanted to see if others have some ideas....  Thanks,  Phill

antonrr90, 2020-05-16:
Funny thing about both BTT & MKS MainBoards, neither brand can manage to get there TFT Ports to work, something that's unusual since TFT has more or less been a standard for over 3 years.

Closed 2020-05-22.

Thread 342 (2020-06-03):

SKR 1.4 Turbo + TMC2209

statiealexandru, 2020-06-03:
Hello,

trying to configure the SKR 1.4 Turbo + TMC2209 setup.

Apparently everything is working OK, yet the motor does not move.

The motor is good, the board is powered (jumper set correctly).

Any ideas?

Send: M122
Recv: 		X	Y	Z	E
Recv: Address		0	0	0	0
Recv: Enabled		false	false	false	false
Recv: Set current	800	800	800	800
Recv: RMS current	795	1436	1436	1436
Recv: MAX current	1121	2025	2025	2025
Recv: Run current	25/31	25/31	25/31	25/31
Recv: Hold current	12/31	12/31	12/31	12/31
Recv: CS actual	12/31	0/31	0/31	0/31
Recv: PWM scale	14	0	0	0
Recv: vsense		1=.18	0=.325	0=.325	0=.325
Recv: stealthChop	true	false	false	false
Recv: msteps		16	256	256	256
Recv: tstep		max	0	0	0
Recv: PWM thresh.
Recv: [mm/s]
Recv: OT prewarn	false	false	false	false
Recv: triggered
Recv:  OTP		false	false	false	false
Recv: off time	3	0	0	0
Recv: blank time	24	16	16	16
Recv: hysteresis
Recv:  -end		-1	-3	-3	-3
Recv:  -start		1	1	1	1
Recv: Stallguard thrs	0	0	0	0
Recv: DRVSTATUS	X	Y	Z	E
Recv: sg_result	0	0	0	0
Recv: stst			*	*	*
Recv: olb
Recv: ola
Recv: s2gb
Recv: s2ga
Recv: otpw
Recv: ot
Recv: 157C
Recv: 150C
Recv: 143C
Recv: 120C
Recv: s2vsa
Recv: s2vsb
Recv: Driver registers:
Recv: 		X	0xC0:0C:00:00
Recv: 		Y	0x00:00:00:00	 Bad response!
Recv: 		Z	0x00:00:00:00	 Bad response!
Recv: 		E	0x00:00:00:00	 Bad response!
Recv:
Recv:
Recv: Testing X connection... OK
Recv: Testing Y connection... Error: All LOW
Recv: Testing Z connection... Error: All LOW
Recv: Testing E connection... Error: All LOW
Recv: ok

AncientAEON, 2020-06-07:
I'm having this same issue. I had forgotten about the DIAG pin and my ender5 kept halting on me.
i removed them from the x and y drivers and now it seems to think its actually moving but yet doesnt move.  My bltouch even deploys for the bed to raise bed none of my motors are moving.
i thought this was an issue with my config files or maybe something i messed up with in the firmware but i've gone through every line and have triple checked all of my work. haven't found anything that would suggest otherwise. the confusing thing to me is the on my skr v1.3 i needed jumpers all down the left side under the driver and now i only need 1 on the Misco pin.  it really seems like there should be a jumper in there somewhere. it's like they aren't receiving a signal to move. sorry this isn't much help.

statiealexandru, 2020-06-08:
Hey!

I have figured out the cause, but not the solution.

The driver enable pin is always high. It remains 3.3v when it should be enabled.

I have desoldered the enabled pin and connected it to a ground pin on the driver and the motor moved normally.

However, in search for a permanent fix i have tried editing the marlin code, even setting the pin to low manually and it does not really work. Something is pulling it up.

Out of desperation i have connected the enable pin (still connected) to a ground pin on the mainboard and that resulted in smoke and a fried board. DO NOT do the same mistake. A software fix is needed. I’ve opened the same issue on the Marlin github repo and ordered another board...

statiealexandru, 2020-06-08:
Possible solution i’ve got on another thread:

You have disabled the dedicated enabled pins.
Please read the following and disable it in your Configuration_adv.h

/**
   * Software enable
   *
   * Use for drivers that do not use a dedicated enable pin, but rather handle the same
   * function through a communication line such as SPI or UART.
   */
  #define SOFTWARE_DRIVER_ENABLE

AncientAEON, since you have a functional board and i don’t have one anymore, could you please test this out?

AncientAEON, 2020-06-08:
Yea I can test it this afternoon when I get off work. Thanks. That line does ring a bell, not sure if it is enabled but I'll definitely look. I also order new 2225's to see if maybe it's the 2209's that are the problem.

Will update you on the code in about 10hrs
The drivers will be here tomorrow.

Thanks for the help

statiealexandru, 2020-06-09:
Solved with the provided config

Closed 2020-06-09.

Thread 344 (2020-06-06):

SKR 1.4 turbo with TMC5160 all high errors

Mace-maker, 2020-06-06:
Hi,
Just installed my new board and drivers with fresh Marlin 2.0.x bug fix based Kay3D cheetah 5.0 firmware on my Ender 5 plus according to Tripod’s Garage YouTube tutorial with the difference being that Tripod has TMC2208 drivers. I also have the TFT3.5 screen and have flashed the unified firmware on it.
I get all high errors and don’t know what to do about this?

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

Mace-maker, 2020-06-07:
Since last post I’ve reflashed with debugging M43 gives the following
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

I’ve soldered clk to ground on one driver and raised the clk pin out of play with precise heating using a soldering iron, no difference....

Mace-maker, 2020-06-09:
No one?

Quinnthouzand, 2020-06-17:
I'm having the same issue ;(

Mace-maker, 2020-06-17:
There’s got to be a way to fix this?!

Mace-maker, 2020-06-25:
Finally, finally, finally.

The BTT pin picture in the manual describes TMC5160 SPI as:
XCS pin 1.10
YCS pin 1.9
ZCS pin 1.8
E0CS pin 1.4
MISO pin 0.5
MOSI pin 1.17
SCK pin 0.4

As a Homo sapiens logicus maximus, for the life of me, I cannot understand that they don’t write what they mean:
XCS pin P1_10
YCS pin 1_09
ZCS pin 1_08
E0 pin 1.04
MISO pin 0.05
MOSI pin 1.17
SCK pin 0.04

No, I won’t accept any flack from electronics nuts that this is just how pins are described in the lingo, complete b.s., point. 1.9 is not 1.09, jeez.

To be clear, you have to:
- Change X_CS_PIN etc line 129 onward in pins_BTT_SKR_V1_4.h
-  Make sure Z_MIN_PROBE is set to P0_10 in all configuration files
- By the way do NOT change the -1 values in configuration_adv.h from line 2270 onward by the way, leave them uncommented as well.

Side note, to upload directly to the board without SD card set line 415 Configuration.h SERIAL_PORT to -1 and SERIAL_PORT_2 to 0 in line 421.

Oh yeah, I also changed the printer name to “Hail Mary, mother of God, please just work!”

tca72, 2021-03-19:
Hello
I also notice that if you disable (comment) #define TMC_USE_SW_SPI  with TMC5160 the ALL HIGH error occurs.

Mace-maker, 2021-03-19:
> Hello
> I also notice that if you disable (comment) #define TMC_USE_SW_SPI with TMC5160 the ALL HIGH error occurs.

Yes, I've since figured out that you have to set this in configuration_adv.h =>

   * Software option for SPI driven drivers (TMC2130, TMC2160, TMC2660, TMC5130 and TMC5160).
   * The default SW SPI pins are defined the respective pins files,
   * but you can override or define them here.
   */
  #define TMC_USE_SW_SPI
  #define TMC_SW_MOSI       P1_17
  #define TMC_SW_MISO       P0_05
  #define TMC_SW_SCK        P0_04

And then everything will work for BTT SPI drivers, TMC5160 and the TMC2130

Pity they just don't add this to the instructions, this is all you have to do.

Closed 2020-08-19.

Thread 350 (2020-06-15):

[SKR 1.4 TURBO] GPIO connection to RPI

minikN, 2020-06-15:
Hello,

I can't for the life of me figure out what I'm doing wrong connection an RPI to my SKR 1.4 using the GPIO pins. I'm using this picture from the manual as a reference:

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,

A pin layout for the RPI can be found [here](https://pinout.xyz/).

I connected it like this:
| RPI | SKR 1.4 |
|-|-|
| 6 (Ground) | GND (TFT) |
| 7 BCM 14 (TXD) | RXD (TFT) |
| 8 BCM 15 (RXD) | TXD (TFT) |

I'm pretty sure I wired it up correctly. I did the following changes to the RPI:

In `/boot/config.txt` I added:
```
enable_uart=1
dtoverlay=pi3-miniuart-bt
```

In `/boot/cmdline.txt` I removed:
```
console=serial0,115200
```

In addition I did:
```
sudo systemctl disable serial-getty@ttyS0.service
```
I then restarted the PI.
In Marlin I changed the following:

In `Configuration.h`:
```
/**
 * Select the serial port on the board to use for communication with the host.
 * This allows the connection of wireless adapters (for instance) to non-default port pins.
 * Serial port -1 is the USB emulated serial port, if available.
 * Note: The first serial port (-1 or 0) will always be used by the Arduino bootloader.
 *
 * :[-1, 0, 1, 2, 3, 4, 5, 6, 7]
 */
#define SERIAL_PORT -1

/**
 * Select a secondary serial port on the board to use for communication with the host.
 * :[-1, 0, 1, 2, 3, 4, 5, 6, 7]
 */
#define SERIAL_PORT_2 0

/**
 * This setting determines the communication speed of the printer.
 *
 * 250000 works in most cases, but you might try a lower speed if
 * you commonly experience drop-outs during host printing.
 * You may try up to 1000000 to speed up SD file transfer.
 *
 * :[2400, 9600, 19200, 38400, 57600, 115200, 250000, 500000, 1000000]
 */
#define BAUDRATE 115200
```

I then added the serial port `/dev/ttyAMA0` to OctoPrint:
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

Here comes the weird part: When I did this for the first time I was able to connect to my printer via OctoPrint (just once). I thought I would try to change the baudrate to `250000` just to see if it would work. I changed it in Marlin and in OctoPrint accordingly. It didn't work (for whatever reason). Then I changed it back to `115200`. Besides that I didn't touch anything else. However ever since that single successfull connection it won't connect again no matter how I tinker with it. I don't think this is an issie with the RPI but with the printer. This is the terminal output when tryint to connect:

```
Connecting to: /dev/ttyAMA0
Changing monitoring state from "Offline" to "Opening serial port"
Connected to: Serial<id=0x67c792f0, open=True>(port='/dev/ttyAMA0', baudrate=115200, bytesize=8, parity='N', stopbits=1, timeout=10.0, xonxoff=False, rtscts=False, dsrdtr=False), starting monitor
Changing monitoring state from "Opening serial port" to "Connecting"
Send: N0 M110 N0*125
No answer from the printer within the connection timeout, trying another hello
Send: N0 M110 N0*125
There was a timeout while trying to connect to the printer
Changing monitoring state from "Connecting" to "Offline"
Connection closed, closing down monitor
```

I also tried re-initializing the EEPROM with a `M502` followed by a `M500` (after switching back to USB connection).

Can anyone help me with this?

Tomblarom, 2020-06-21:
Since you're using a Raspberry, why don't you switch to Klipper? It's working perfectly fine, you're able to change the config in OctoKlipper and you're able to use the processing power of your Pi! :)

I know it's not answering your question, but I don't get it, why people still use Marlin :D

minikN, 2020-06-21:
> Since you're using a Raspberry, why don't you switch to Klipper? It's working perfectly fine, you're able to change the config in OctoKlipper and you're able to use the processing power of your Pi! :)
>
> I know it's not answering your question, but I don't get it, why people still use Marlin :D

Im currently not interested in looking into Klipper. Im new to 3d printing and I'd lile to fully understand my setup before switching to something new.

zonalimitatore, 2020-07-02:
But the pin you write are correct? pin8 tx0 pin10 rx0, not 7 and 8

WhatTakWhat, 2021-01-10:
> Since you're using a Raspberry, why don't you switch to Klipper? It's working perfectly fine, you're able to change the config in OctoKlipper and you're able to use the processing power of your Pi! :)
>
> I know it's not answering your question, but I don't get it, why people still use Marlin :D

xD
For me Klipper doesn't allow to use usb for connection RPI 4 to skr 1.4 turbo (btw octopi can see same skr plate with Marlin frome same RPI 4).
I want to use Klipper, but I can't. If you know how to change bin compiler in Klipper (to make him work correctly) - please help.
Even lsusb can't show me any changes on dev directory when I use Klipper firmware on SKR 1.4 Turbo. Maybe you know other workaround?

So I use Marlin because it works. Not because I want to.

heatvent, 2021-01-24:
Hi, suffering through the same issue.  How was this resolved?

WhatTakWhat, 2021-03-16:
> Hi, suffering through the same issue.  How was this resolved?

Hello! In my case:

re-install Marlin;
Apply base config;
Install Klipper;
Follow Klipper instructions.

It seems like Marlin have more power in firmware, even if Klipper installed.

Closed 2021-01-16.

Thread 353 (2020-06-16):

Outage Recovery: PRINTED HALTED Error

xolutronic, 2020-06-16:
I have a SKR v1.4 Turbo running Marlin V2.0.5.3 with the BTT UPS 24V module and the TFT35-E3 V3.0.

Out of curiosity I selected the "Power Outage" option through the LCD running in Marlin mode. Right after that I got the message on-screen:

Outage Recovery:
PRINTER HALTED
Please Reset

I have tried resetting the board, through the Reset in the TFT35 board and also the reset in the SKR board, but it always gets back to the same error after booting up. I have tried completely removing the power supply and restarting, but I keep getting the same issue. I tried updating the firmware, but I still get the same issue.

My guess is that something was stored in memory when I chose the "Power Outage" option and it is preventing the firmware from running as it should.

How can I fix this?

xolutronic, 2020-06-17:
I was able to fix the issue as follows:

First, to be able to boot without the PRINTER HALTED issue, I switch from FLASH_EEPROM_EMULTATION to SDCARD_EEPROM_EMULATION. This is achieved by modifying the corresponding pins_BTT_SKR_V1_4.h or pins_BTT_SKR_V1_4_TURBO.h file found under the /pins/lpc1768 or /pins/lpc1769 directories respectively.

So the issue was that I activated the Power Loss Recovery but I had misconfigured the POWER_LOSS_PIN. I was following the instructions in the BTT UPS 24V manual which indicated to use P1_26, but I had the cable physically connected to the E1DET connector (and the correct signal pin was P1_25). This resulted in the Power Loss State being triggered every time after booting up.

Closed 2020-06-17.

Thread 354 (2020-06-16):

SKR1.4 Filament Sensor not responding / stop during Print

elmolinger, 2020-06-16:
Hi Guys,

I try to get my Runout Sensor running on the SKR1.4. Unfortunately so far without success.

I went through almost all configurations. The sensor works and IO voltage was measured at the sensor out.

my FRS config
`#define FILAMENT_RUNOUT_SENSOR`
`#if ENABLED(FILAMENT_RUNOUT_SENSOR)`
 ` #define NUM_RUNOUT_SENSORS   1     // Number of sensors, up to one per extruder. Define a FIL_RUNOUT#_PIN for each.`
  `#define FIL_RUNOUT_INVERTING false // Set to true to invert the logic of the sensor.`
`  #define FIL_RUNOUT_PULLUP          // Use internal pullup for filament runout pins.`
 ` //#define FIL_RUNOUT_PULLDOWN      // Use internal pulldown for filament runout pins.`
`  #define FILAMENT_RUNOUT_SCRIPT "M600"`
`  #define FILAMENT_RUNOUT_DISTANCE_MM 7`
`  #ifdef FILAMENT_RUNOUT_DISTANCE_MM`
`    //#define FILAMENT_MOTION_SENSOR`

Unfortunately I didn't get any signal via M119 at runout pin P1_26.
Only when I set FIL_RUNOUT_PIN to P1_25 did M119 display triggered / open during the test.
`#define FIL_RUNOUT_PIN                     P1_25  // E0DET`
`#define FIL_RUNOUT2_PIN                    P1_26  // E1DET`
>Reporting endstop status
x_min: open
y_min: open
z_min: TRIGGERED
z_probe: TRIGGERED
filament: TRIGGERED
 m119
SENDING:M119
Reporting endstop status
x_min: open
y_min: open
z_min: TRIGGERED
z_probe: TRIGGERED
filament: open
SENDING:M412
echo:Filament runout ON
Filament runout distance (mm): 7.00

Does anyone have experience here how to set the sensor correctly?

Best regards

spiffy781, 2020-07-11:
Same issue,  SKR 1.4 machine will start print then after 10/15 mm of extrusion will go into filament change mode.

Closed 2020-06-19.

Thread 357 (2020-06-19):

SKR1.4-Turbo + TMC2209 + Marlin 2.0.x + StealthChop issue

DustinSnijders, 2020-06-19:
Hi All,

I'm running a configuration as above (skr1.4 + tmc2209) on Marlin 2. In advance everything seems to work fine, no compiling issues and all the M-commands works as expected. In past I used a SKR1.3 board with TMC2130's. No issue at all. I only switched the board and the steppendrivers right now, due to some heath issues (Delta printer) with the TMC2130's and I like te reuse the board for another (carthesian) printer.

What is the issue; when I print with SpreadCycle activated, everything is okay. Standard deviation is very ok (0.006) and the printresults are like I expect...even better. The SpreadCycle is a bit noisy, you can almost hear the data whispering, but still better than without compensation... :-) When I activate StealthChop (M569 S1 X Y Z) an oase of silence, but if I send for example G28 or a G0 Z50 to the  printer, it moves nice and without noise, in a completely weird direction, unlogical sequenced, unpredictable and finishes with an error: printer halted.

Does anyone recognise this issue? SpreadCycle: Working top (bit noisy) and SteathChop: quiet but not manageble en giving errors like:

Recv: Error:Printer halted. kill() called!
Changing monitoring state from "Operational" to "Error: Printer halted. kill() called!"
Send: M112
Send: N2 M112*35
Send: N3 M104 T0 S0*34
Send: N4 M140 S0*97
Changing monitoring state from "Error: Printer halted. kill() called!" to "Offline (Error: Printer halted. kill() called!)"

I attached my conf files:

[Marlin 2.0.6.zip](https://github.com/bigtreetech/BIGTREETECH-SKR-V1.3/files/4804341/Marlin.2.0.6.zip)

I also tried the not-nightly and not-bèta versions of Marlin, but there was no difference. I hope that someone can help me.

Cheers,
Dustin

DustinSnijders, 2020-06-20:
By the way, I don't see errors when I switch to StealthChop. Really weird. Someone any clue?

DustinSnijders, 2020-06-21:
Update: I changed the TCM2209's for my older TCM2130's...exactly te same issue as described above...
SPI instead of UART, no difference and still no clue...help?!

DustinSnijders, 2020-06-21:
Update: Reflowing the LPC1769 did not help as well...

I had a brainwave; UART control of the stepperdrivers is using a serial bus. My display is using a serial connection as well, maybee is both  the data conflicting...nope. I even did 'greyed out'  the display, but no solution...

DustinSnijders, 2020-06-26:
Many hours later....I was apparently searching in the wrong direction. At the end I decided to use another earlier distri I used before with my SKR1.3.  It is a combination of the Bigtreetech distri and Marlin 2.0.5 examples config files for my Delta (Kossel XL 80cm) I merged in the past. I changed the board and some other small settings in relation to the LPC1769 and the 1.4 HW
I'm also using the rest of the source of the 2.0.5 Marlin distri. It seems that there is a slight difference what haves effect on the stealthchop function. It works fine now...

DustinSnijders, 2020-06-26:
So i close the case...thanks for all the support ;-)

Closed 2020-06-26.

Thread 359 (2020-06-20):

SKR 1.4 with Marlin 2.0.5.3 - Extruder (LV8729) not working !!

Flyingmatdes, 2020-06-20:
Hello all !

I'm using an SKR 1.4 (non-turbo) with TMC2209 on X, Y and Z axis. These TMC2209 are in UART mode. For the extruder, I have a LV8729 configured to be 1/16 steps.

At first try, the BL Touch wasn't working but all axis where nice and quiet. I finally found the solution and make the BLT working. I re-started from scratch and was able to have all axis working with bl-touch, but this time, the steppers are really noisy.. pff anyway..

the problem is the extruder is still not working..

I tried:

- Use the E-motor on another axis: works ! so it's not the wiring.
- Use another TMC2209 instead of the LV8729... well nothing happen under stealthchop, but in spreadcycle I got a really strange behavior... the motor was going one step left, then one step right (oscilating)...
- change minimum steps: no change
- change chopper mode: no change
- change steps config for LV8729: no change
- activate the 50/50 wave: no change
- enable/diable stealthchop_E: no change

I will try to place the LV8729 on another axis, but I'm really sure the driver isn't the issue. The vref on the LV8729 is set at 0.6v. I also have a second LV8729 and.. same issue, the extruder still not working.

My LA is disabled !

Please help ! I don't know what to do now !! I tried using bugfix_2.0.X and also 2.0.5.3 but without success ! is it the board that has an issue ???

 thanks for your help !!

Flyingmatdes, 2020-06-22:
After quite investiguation... I found the issue ! a bad soldering. there where a short-circuit between two extruder pins on the board ! how come it passed the QC ??? I re-did the soldering and everything is working great now !

Closed 2020-06-22.

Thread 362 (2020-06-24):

BL-touch servo+probe port

hopatz, 2020-06-24:
Hi, can i use this port/pin probe+servos ??
I wanna install BL-touch..

Thank you

zonalimitatore, 2020-07-02:
What kind of bug?
Whre do you wanna connect it?

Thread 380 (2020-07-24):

Hotends and PWM fans stopped working

Plateaus, 2020-07-24:
Hello!

My board is working well to the point of heating up the bed/nozzle or using PWM fans. I used it for two months with no issues.

I replaced the fuses just to be sure but that did not work. I see no internal damage or burned components.

Please help

Tomthi, 2020-07-25:
Have you tested if the HE / Fan terminals are showing voltage?

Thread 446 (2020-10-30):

Cant add more than 3 drivers

vinoudropdrop, 2020-10-30:
Hi! I'm something like noob with 3d printing and configurate it.
First, about the configuration :
- SKR v1.4 Turbo
- Marlin 2.x bugfix
- RepRapDiscount Full Graphic Smart Controler
- 5x : DRV8825 v2.0 BTT ( with E1 as dual Z  by modify line `#define NUM_Z_STEPPER_DRIVERS 2` in Configuration_adv.h)
- 5x : 17HS4401
- PSU : Leadstar S-360-24 (24v/15A)
- Jhead v6
- Redrex Dual Drive extruder
- Hotbed not connected at this time
And, I have an issue.
When I try to plug more than 3 drivers, nothing move.
If I plug only one, two, or three drivers whatever if it is on X, Y, Z, E1 or E2, I can move stepsmotors.
But if I plug 4 or all the 5 drivers in, no one motor move again.
I have searched in the issues there, and I didn't found any result to help me.
Have you an idea about what to check?

vinoudropdrop, 2020-10-30:
Ok, I found the mistake.
All jumpers behind steppers were on the right (capacitor side). Jumped all to the left and now it work!
I close the Issue

Closed 2020-10-30.

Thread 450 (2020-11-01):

X axis stalls wont travel / home

iHover01, 2020-11-01:
I just installed SKR V1.4 Turbo board with TMC 5160 stepper drivers on all axis.  when I home all the axis work fine except for the x axis. it begins moving to home but stops traveling after moving a 10-20 mm. If I move it close to the switch it it homes but it I try bed leveling following that it has the same behaviors, it moves a few mm and then stops. I have all the TMC settings for this axis setup the same as the Y axis which works without any issues.

mpapam, 2020-11-14:
Have been trying for hours and hours to make my TMC5160 to work on SKR without any success, no movement at all. Can you please share your configuration.h and configuration_adv.h files along with your hardware setup?
Regarding your issue I suggest you exchange drivers with Y or Z axis to see whether it is a faulty driver issue

iHover01, 2020-11-15:
Sorry though I closed this. It appears to have been an issue with a cable

Closed 2020-11-15.

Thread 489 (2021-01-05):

how do the mosfets work skr 1.4

nusilor, 2021-01-05:
All my mosfets turned on without a signal. This blew q1 q4 and my hot-end burnt up that was running on q3.
Since u6 seemed to control the gate i removed it, but they are all still active. does u6 pull the gate to ground, if not i cant seem to find where this 5v (q3,q1 and .3 on q2) signal is coming from, and it doesn't seem to be shorted to any of the 5v rails. the schematic says the only path on gate is u6.
when i cut the legs of the mosfest  drain to source the lights go out also when i cut the leg to gate

nusilor, 2021-01-05:
ok turns out the led was was just out on the one one with the gate leg cut and all the mosfets are blown

Closed 2021-01-05.

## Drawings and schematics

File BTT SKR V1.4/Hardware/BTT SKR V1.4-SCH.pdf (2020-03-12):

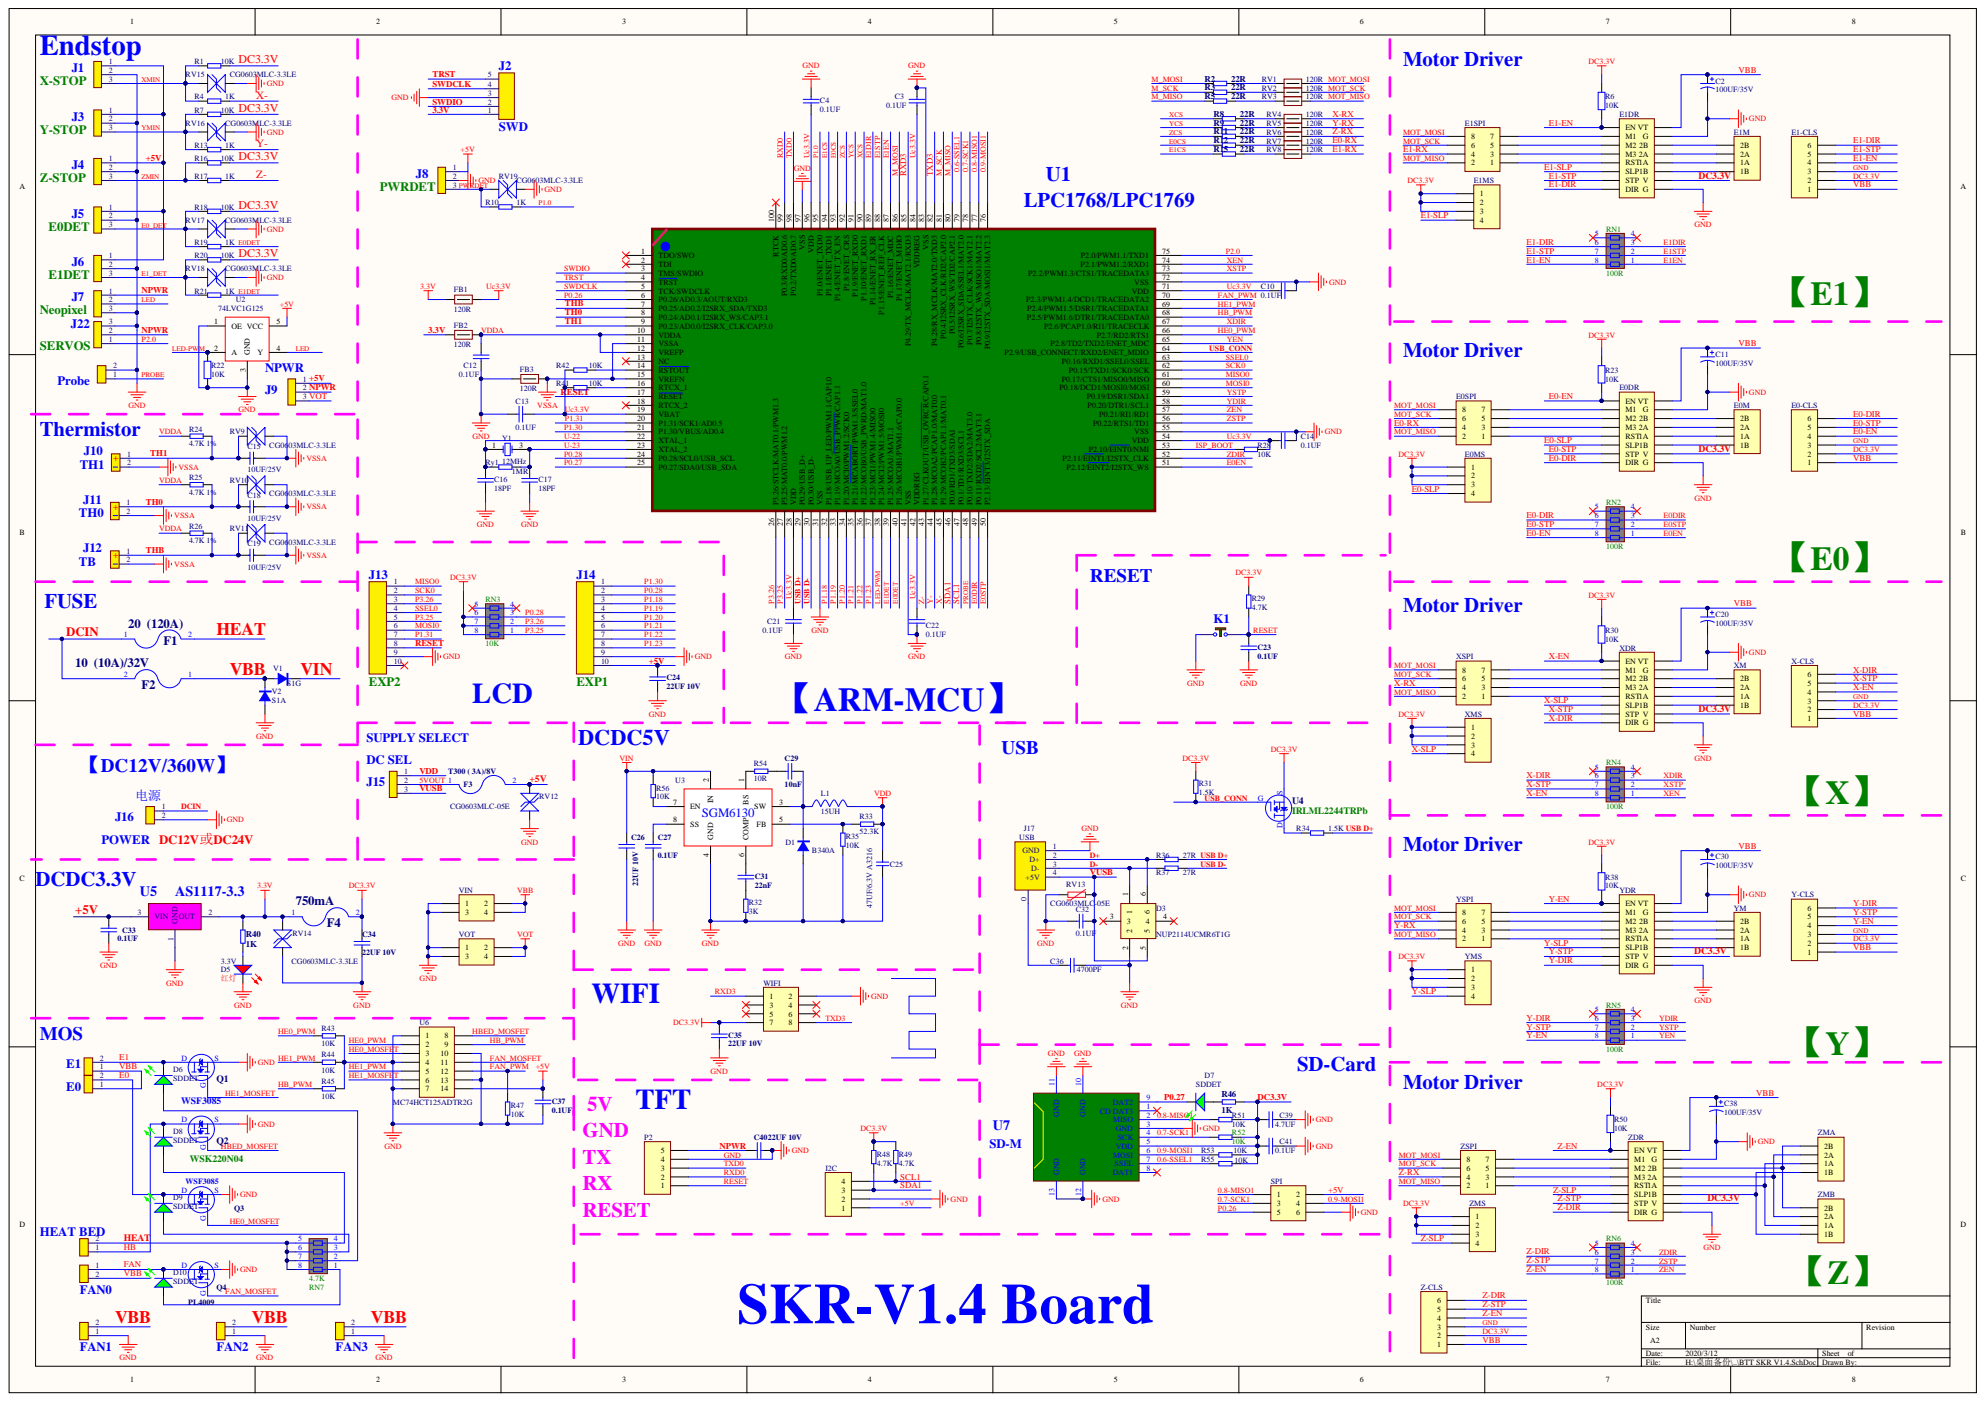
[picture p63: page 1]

P0.9/I2STX_SDA/MOSI1/MAT2.3 76 P0.8/I2STX_WS/MISO1/MAT2.2 77 P0.7/I2STX_CLK/SCK1/MAT2.1 78 P0.6/I2SRX_SDA/SSEL1/MAT2.0 79 P0.5/I2SRX_WS/TD2/CAP2.1 80 P0.4/I2SRX_CLK/RD2/CAP2.0 81 P4.28/RX_MCLK/MAT2.0/TXD3 82 VSS 83 VDDREG 84 P4.29/TX_MCLK/MAT2.1/RXD3 85 P1.17/ENET_MDIO 86 P1.16/ENET_MDC 87 P1.15/ENET_REF_CLK 88 P1.14/ENET_RX_ER 89 P1.10/ENET_RXD1 90 P1.9/ENET_RXD0 91 P1.8/ENET_CRS 92 P1.4/ENET_TX_EN 93 P1.1/ENET_TXD1 94 P1.0/ENET_TXD0 95 VDD 96 VSS 97 P0.2/TXD0/AD0.7 98 P0.3/RXD0/AD0.6 99 RTCK 100

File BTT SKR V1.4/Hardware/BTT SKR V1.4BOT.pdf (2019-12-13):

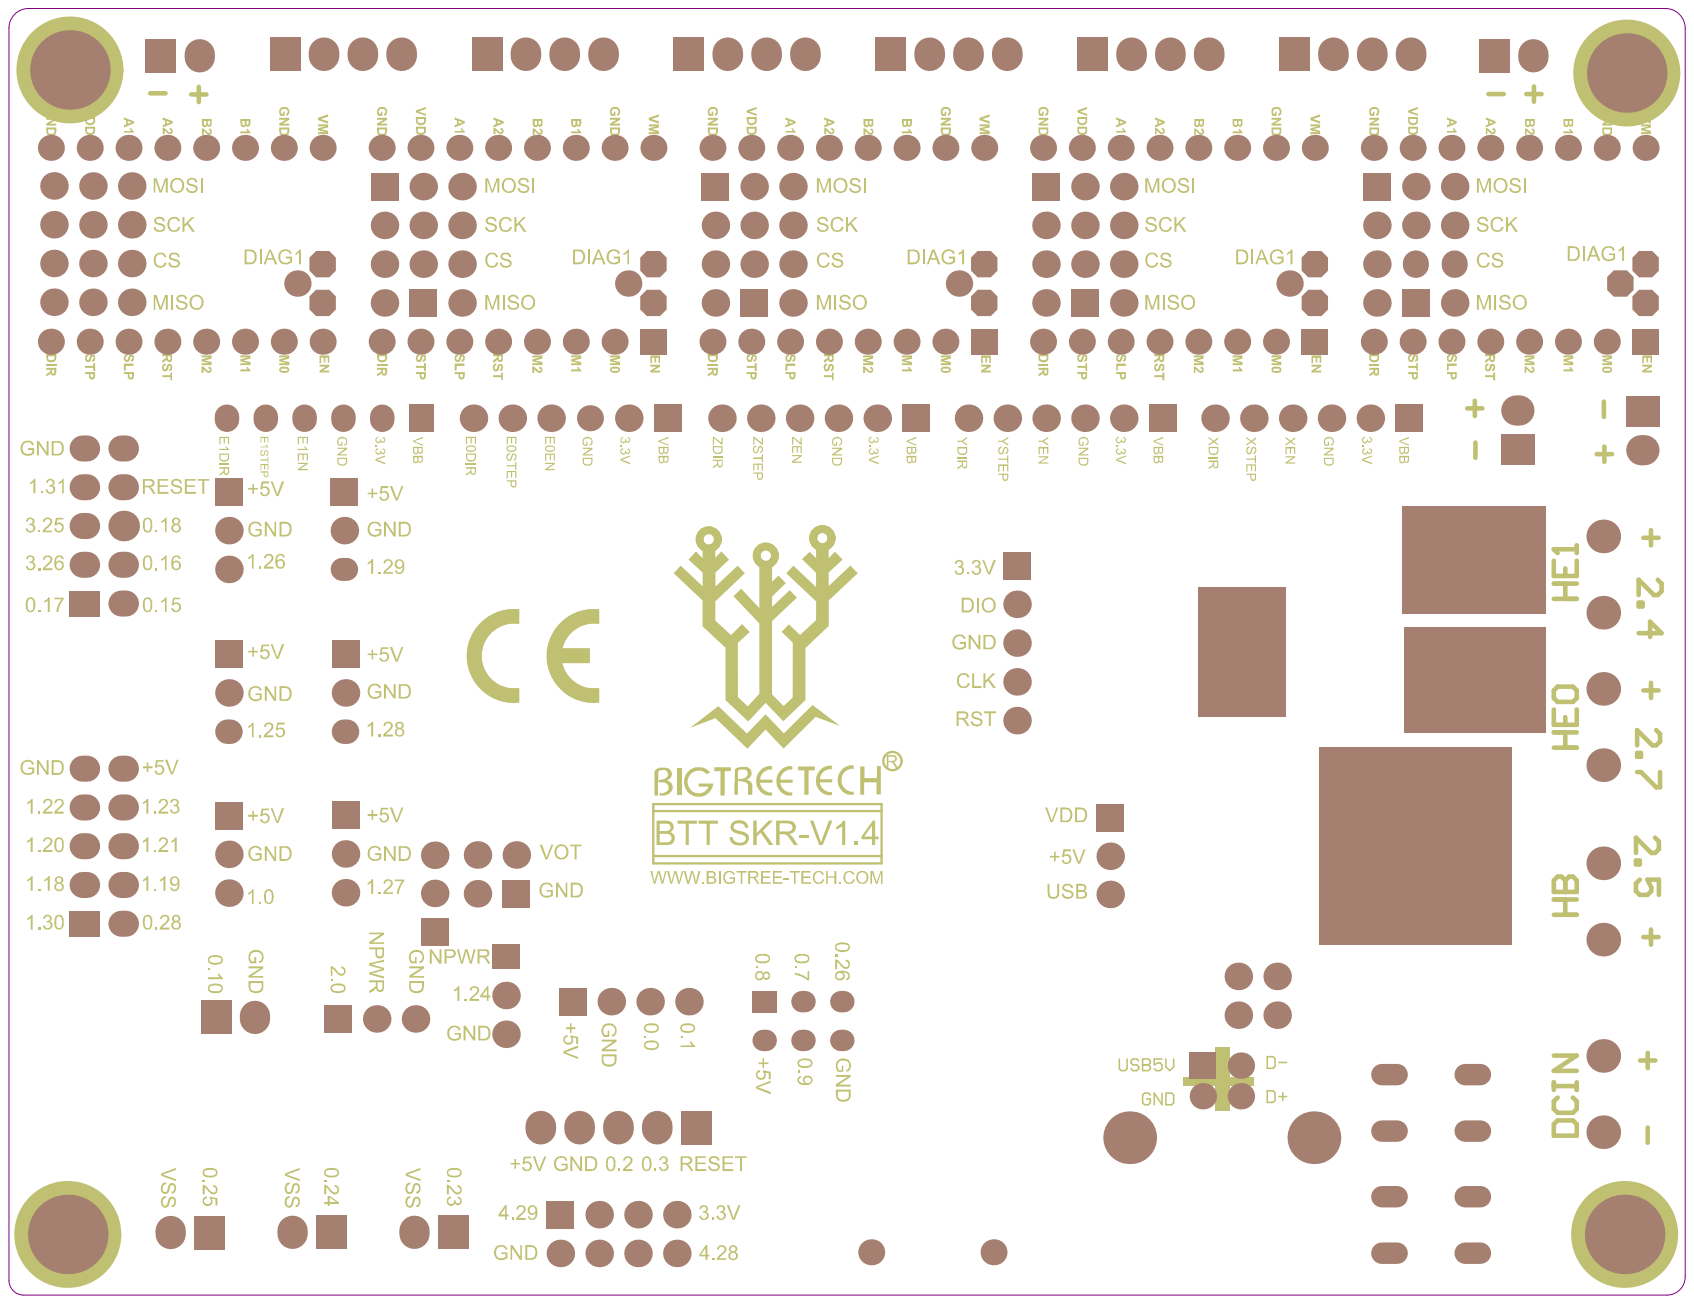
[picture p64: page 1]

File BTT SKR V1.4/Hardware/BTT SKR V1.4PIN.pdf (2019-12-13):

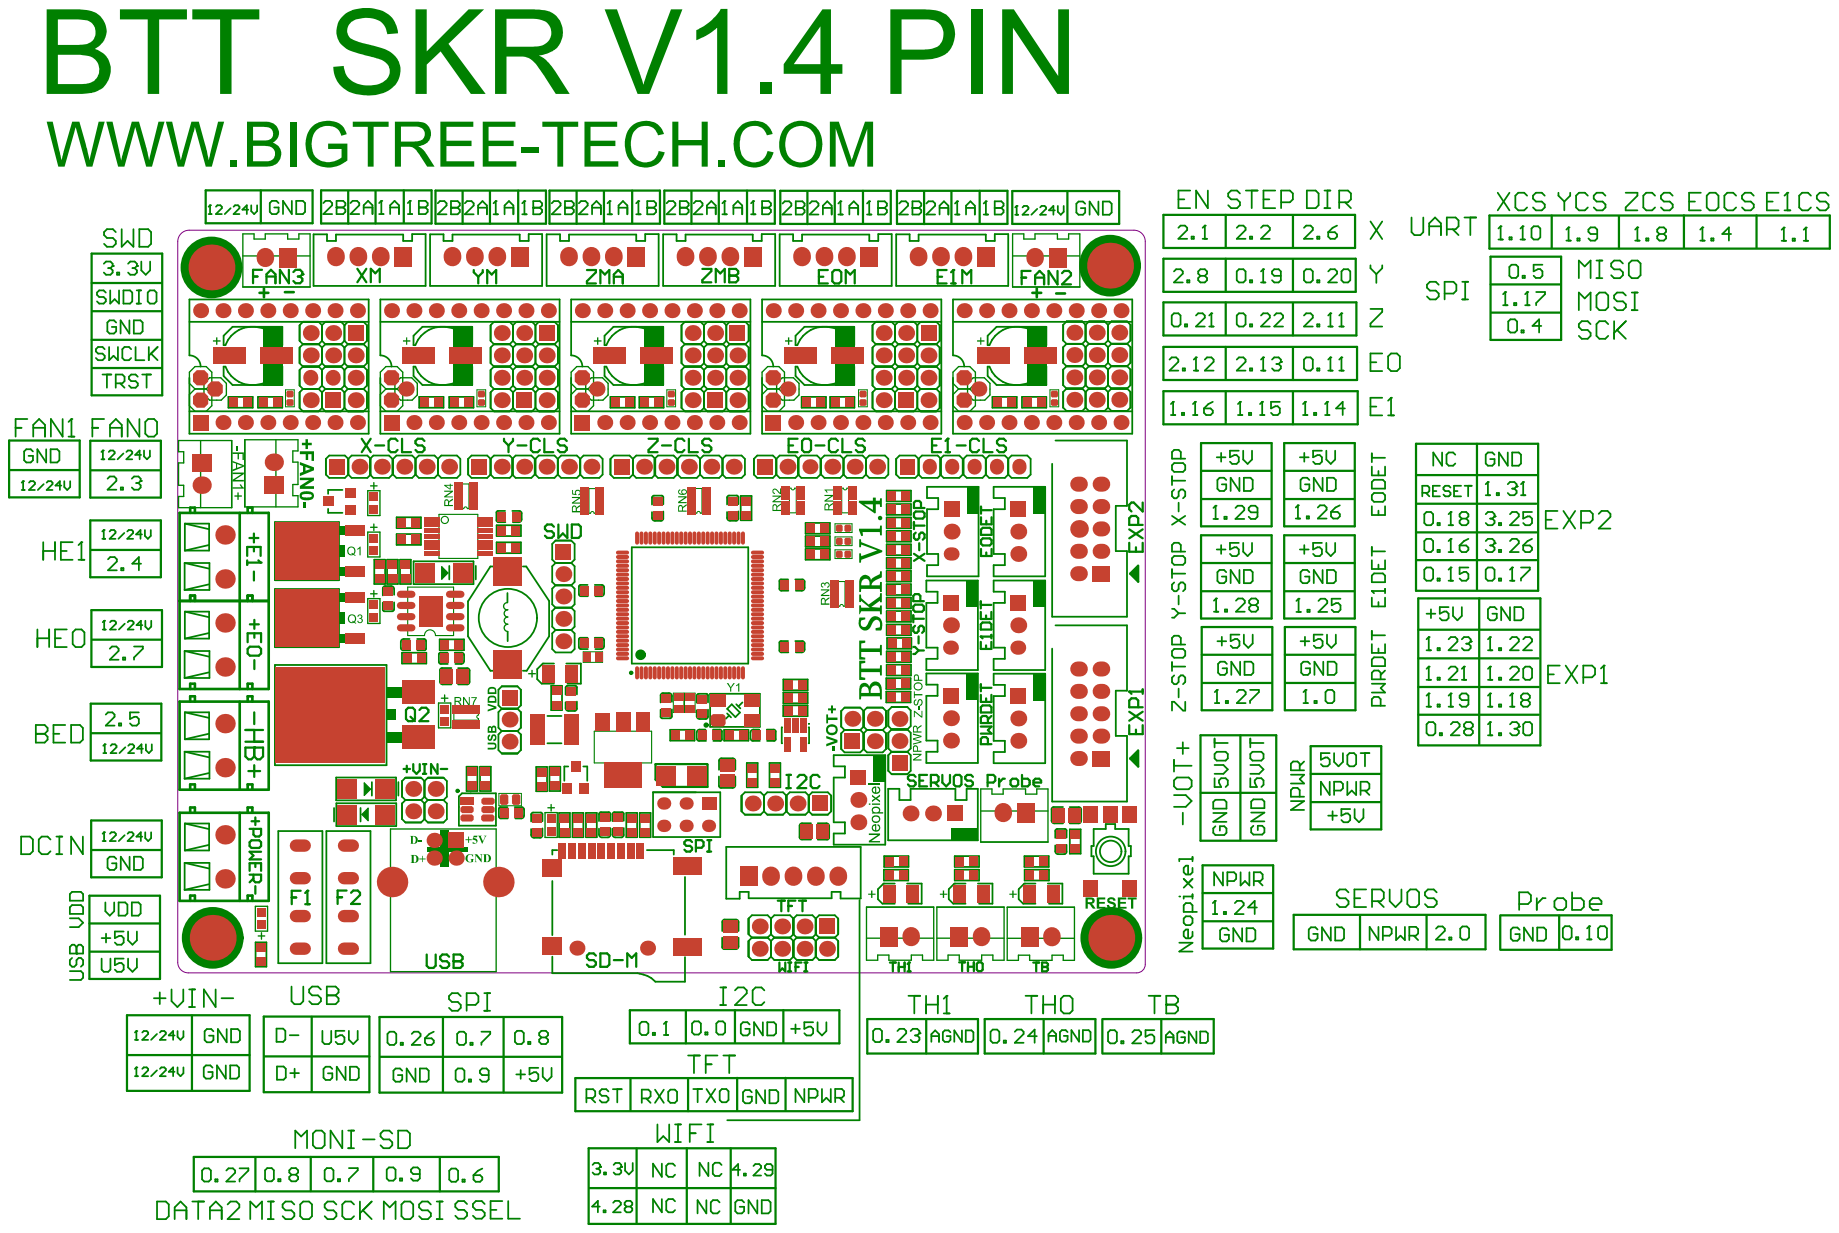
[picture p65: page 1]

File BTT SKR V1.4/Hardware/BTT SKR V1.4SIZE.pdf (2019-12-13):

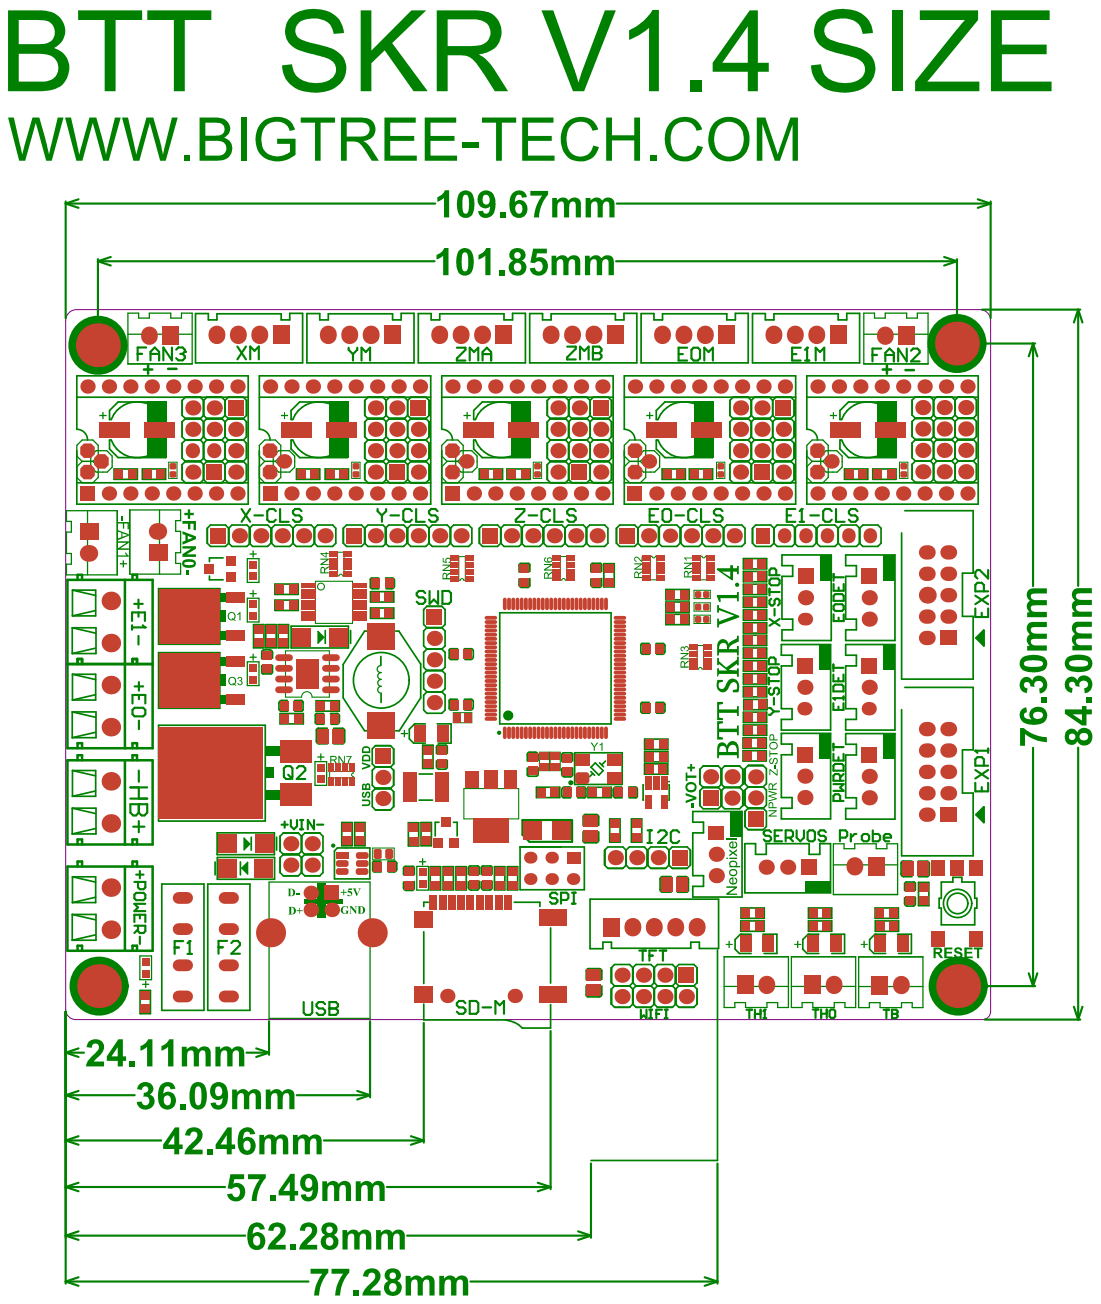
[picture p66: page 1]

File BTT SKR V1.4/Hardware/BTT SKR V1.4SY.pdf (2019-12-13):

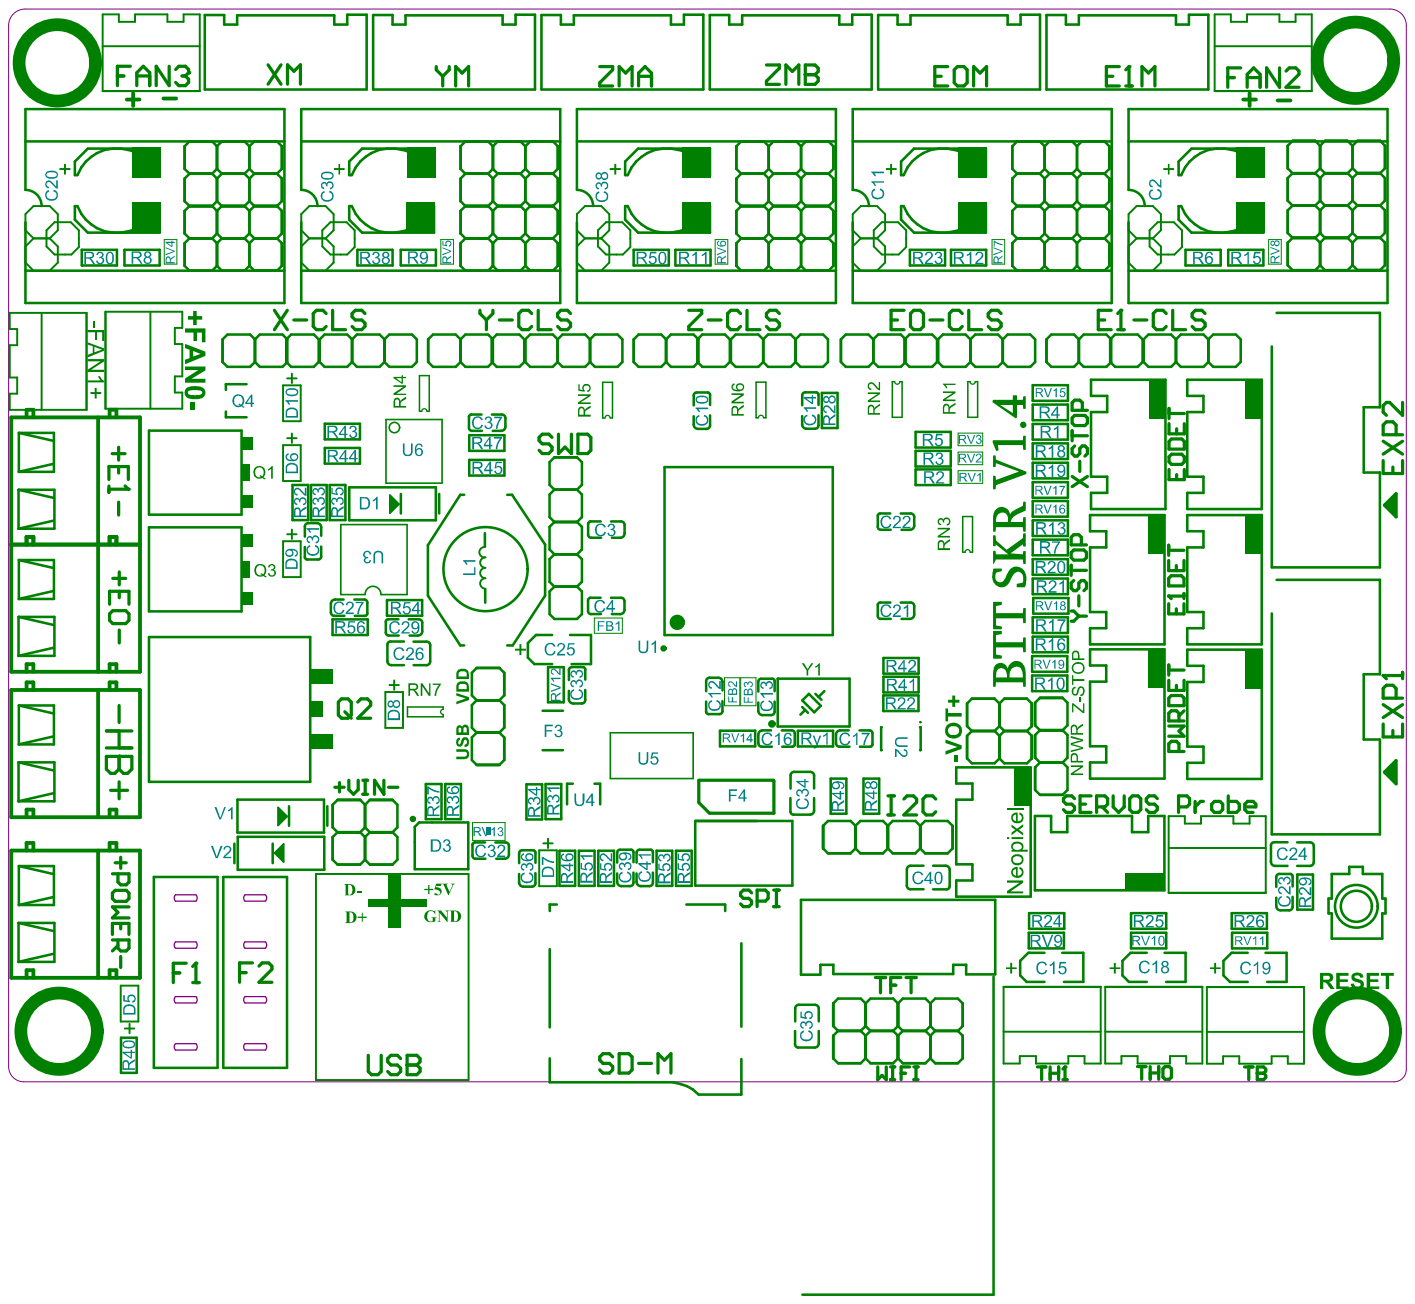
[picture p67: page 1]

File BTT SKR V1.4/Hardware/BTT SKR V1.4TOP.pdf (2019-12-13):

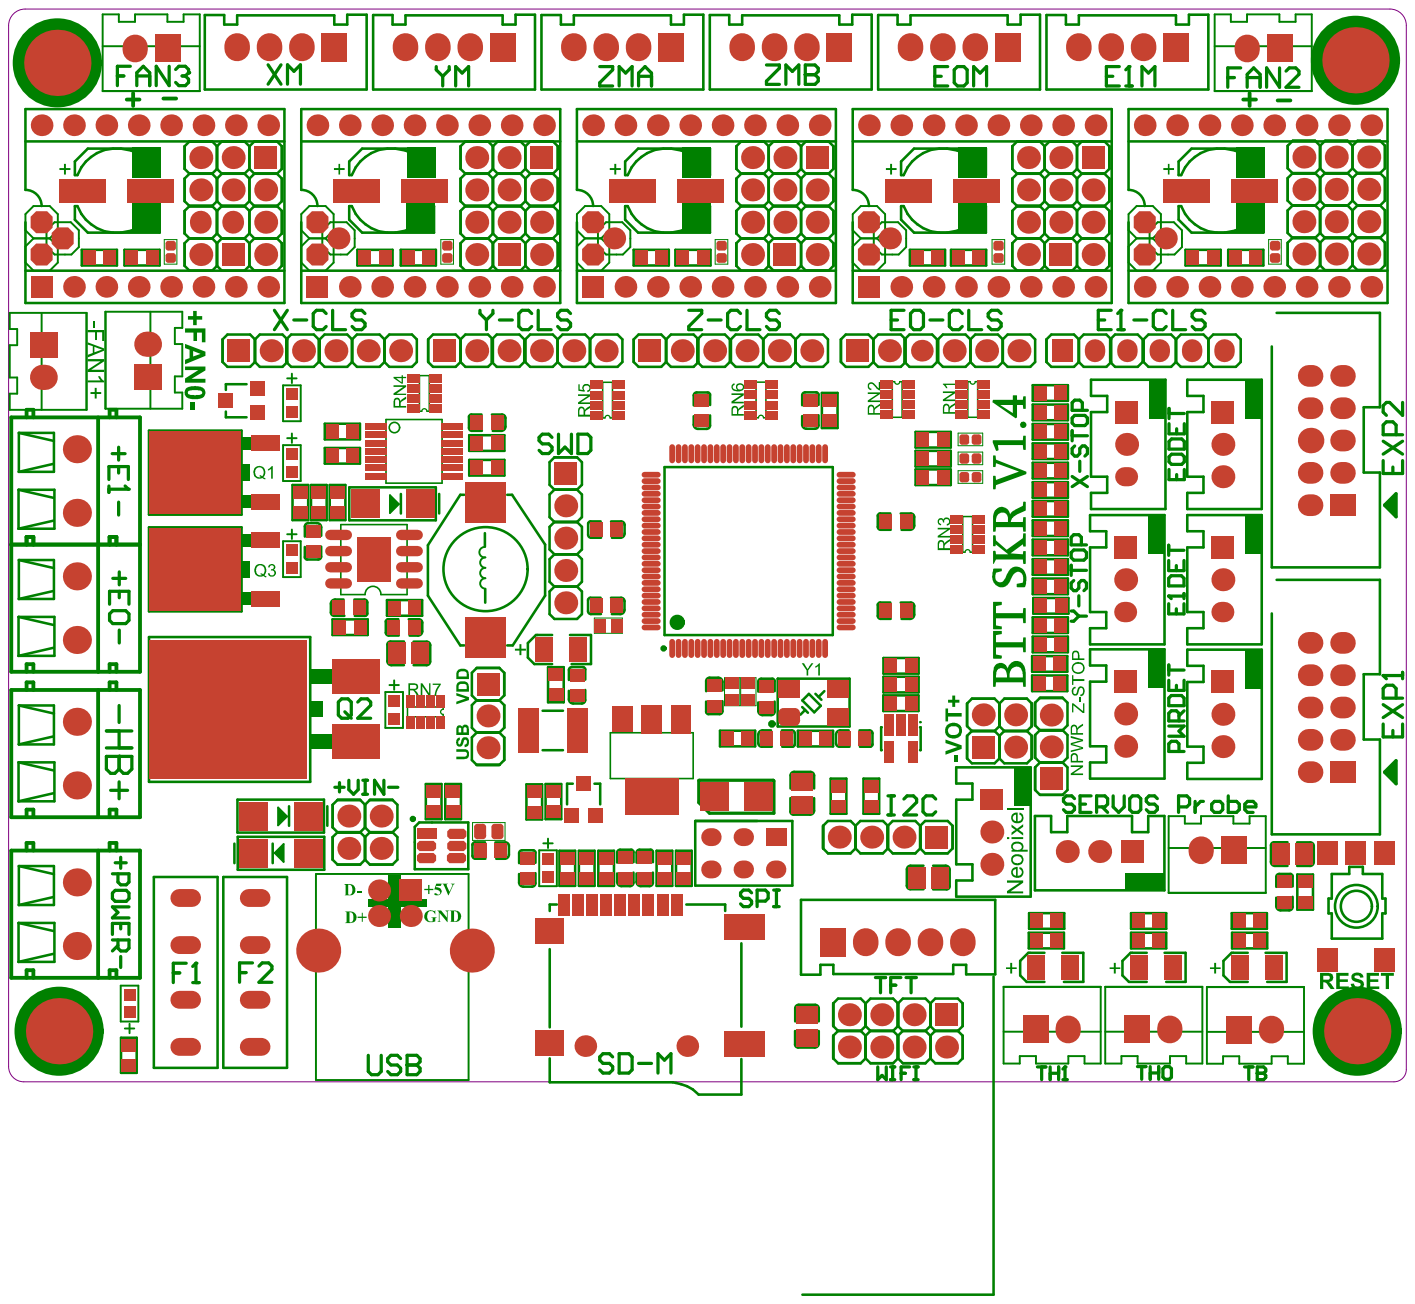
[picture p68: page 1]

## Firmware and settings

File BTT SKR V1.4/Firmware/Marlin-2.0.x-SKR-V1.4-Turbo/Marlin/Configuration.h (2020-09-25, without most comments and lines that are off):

#pragma once
#define CONFIGURATION_H_VERSION 020006
#define STRING_CONFIG_H_AUTHOR "(none, default config)" // Who made the changes.
#define SHOW_BOOTSCREEN
#define SERIAL_PORT -1
#define SERIAL_PORT_2 0
#define BAUDRATE 115200
  #define MOTHERBOARD BOARD_BTT_SKR_V1_4_TURBO
#define EXTRUDERS 1
#define DEFAULT_NOMINAL_FILAMENT_DIA 1.75
#define TEMP_SENSOR_0 1
#define TEMP_SENSOR_1 0
#define TEMP_SENSOR_2 0
#define TEMP_SENSOR_3 0
#define TEMP_SENSOR_4 0
#define TEMP_SENSOR_5 0
#define TEMP_SENSOR_6 0
#define TEMP_SENSOR_7 0
#define TEMP_SENSOR_BED 1
#define TEMP_SENSOR_PROBE 0
#define TEMP_SENSOR_CHAMBER 0
#define DUMMY_THERMISTOR_998_VALUE 25
#define DUMMY_THERMISTOR_999_VALUE 100
#define MAX_REDUNDANT_TEMP_SENSOR_DIFF 10
#define TEMP_RESIDENCY_TIME     10  // (seconds) Time to wait for hotend to "settle" in M109
#define TEMP_WINDOW              1  // (°C) Temperature proximity for the "temperature reached" timer
#define TEMP_HYSTERESIS          3  // (°C) Temperature proximity considered "close enough" to the target
#define TEMP_BED_RESIDENCY_TIME 10  // (seconds) Time to wait for bed to "settle" in M190
#define TEMP_BED_WINDOW          1  // (°C) Temperature proximity for the "temperature reached" timer
#define TEMP_BED_HYSTERESIS      3  // (°C) Temperature proximity considered "close enough" to the target
#define HEATER_0_MINTEMP   5
#define HEATER_1_MINTEMP   5
#define HEATER_2_MINTEMP   5
#define HEATER_3_MINTEMP   5
#define HEATER_4_MINTEMP   5
#define HEATER_5_MINTEMP   5
#define HEATER_6_MINTEMP   5
#define HEATER_7_MINTEMP   5
#define BED_MINTEMP        5
#define HEATER_0_MAXTEMP 275
#define HEATER_1_MAXTEMP 275
#define HEATER_2_MAXTEMP 275
#define HEATER_3_MAXTEMP 275
#define HEATER_4_MAXTEMP 275
#define HEATER_5_MAXTEMP 275
#define HEATER_6_MAXTEMP 275
#define HEATER_7_MAXTEMP 275
#define BED_MAXTEMP      150
#define PIDTEMP
#define BANG_MAX 255     // Limits current to nozzle while in bang-bang mode; 255=full current
#define PID_MAX BANG_MAX // Limits current to nozzle while PID is active (see PID_FUNCTIONAL_RANGE below); 255=full current
#define PID_K1 0.95      // Smoothing factor within any PID loop
  #define DEFAULT_Kp 22.2
  #define DEFAULT_Ki 1.08
  #define DEFAULT_Kd 114
#define MAX_BED_POWER 255 // limits duty cycle to bed; 255=full current
  #define PID_FUNCTIONAL_RANGE 10 // If the temperature difference between the target temperature and the actual temperature
#define PREVENT_COLD_EXTRUSION
#define EXTRUDE_MINTEMP 170
#define PREVENT_LENGTHY_EXTRUDE
#define EXTRUDE_MAXLENGTH 200
#define THERMAL_PROTECTION_HOTENDS // Enable thermal protection for all extruders
#define THERMAL_PROTECTION_BED     // Enable thermal protection for the heated bed
#define THERMAL_PROTECTION_CHAMBER // Enable thermal protection for the heated chamber
#define USE_XMIN_PLUG
#define USE_YMIN_PLUG
#define USE_ZMIN_PLUG
#define ENDSTOPPULLUPS
#define X_MIN_ENDSTOP_INVERTING false // Set to true to invert the logic of the endstop.
#define Y_MIN_ENDSTOP_INVERTING false // Set to true to invert the logic of the endstop.
#define Z_MIN_ENDSTOP_INVERTING false // Set to true to invert the logic of the endstop.
#define X_MAX_ENDSTOP_INVERTING false // Set to true to invert the logic of the endstop.
#define Y_MAX_ENDSTOP_INVERTING false // Set to true to invert the logic of the endstop.
#define Z_MAX_ENDSTOP_INVERTING false // Set to true to invert the logic of the endstop.
#define Z_MIN_PROBE_ENDSTOP_INVERTING false // Set to true to invert the logic of the probe.
#define DEFAULT_AXIS_STEPS_PER_UNIT   { 80, 80, 400, 93 }
#define DEFAULT_MAX_FEEDRATE          { 500, 500, 5, 25 }
#define DEFAULT_MAX_ACCELERATION      { 500, 500, 100, 5000 }
#define DEFAULT_ACCELERATION          500    // X, Y, Z and E acceleration for printing moves
#define DEFAULT_RETRACT_ACCELERATION  500    // E acceleration for retracts
#define DEFAULT_TRAVEL_ACCELERATION   500    // X, Y, Z acceleration for travel (non printing) moves
#define DEFAULT_EJERK    5.0  // May be used by Linear Advance
  #define JUNCTION_DEVIATION_MM 0.013 // (mm) Distance from real junction edge
  #define JD_HANDLE_SMALL_SEGMENTS    // Use curvature estimation instead of just the junction angle
#define Z_MIN_PROBE_USES_Z_MIN_ENDSTOP_PIN
#define NOZZLE_TO_PROBE_OFFSET { 10, 10, 0 }
#define PROBING_MARGIN 10
#define XY_PROBE_SPEED (133*60)
#define Z_PROBE_SPEED_FAST HOMING_FEEDRATE_Z
#define Z_PROBE_SPEED_SLOW (Z_PROBE_SPEED_FAST / 2)
#define Z_CLEARANCE_DEPLOY_PROBE   10 // Z Clearance for Deploy/Stow
#define Z_CLEARANCE_BETWEEN_PROBES  5 // Z Clearance between probe points
#define Z_CLEARANCE_MULTI_PROBE     5 // Z Clearance between multiple probes
#define Z_PROBE_LOW_POINT          -2 // Farthest distance below the trigger-point to go before stopping
#define Z_PROBE_OFFSET_RANGE_MIN -20
#define Z_PROBE_OFFSET_RANGE_MAX 20
#define X_ENABLE_ON 0
#define Y_ENABLE_ON 0
#define Z_ENABLE_ON 0
#define E_ENABLE_ON 0 // For all extruders
#define DISABLE_X false
#define DISABLE_Y false
#define DISABLE_Z false
#define DISABLE_E false             // Disable the extruder when not stepping
#define DISABLE_INACTIVE_EXTRUDER   // Keep only the active extruder enabled
#define INVERT_X_DIR false
#define INVERT_Y_DIR false
#define INVERT_Z_DIR true
#define INVERT_E0_DIR false
#define INVERT_E1_DIR false
#define INVERT_E2_DIR false
#define INVERT_E3_DIR false
#define INVERT_E4_DIR false
#define INVERT_E5_DIR false
#define INVERT_E6_DIR false
#define INVERT_E7_DIR false
#define X_HOME_DIR -1
#define Y_HOME_DIR -1
#define Z_HOME_DIR -1
#define X_BED_SIZE 200
#define Y_BED_SIZE 200
#define X_MIN_POS 0
#define Y_MIN_POS 0
#define Z_MIN_POS 0
#define X_MAX_POS X_BED_SIZE
#define Y_MAX_POS Y_BED_SIZE
#define Z_MAX_POS 200
#define MIN_SOFTWARE_ENDSTOPS
  #define MIN_SOFTWARE_ENDSTOP_X
  #define MIN_SOFTWARE_ENDSTOP_Y
  #define MIN_SOFTWARE_ENDSTOP_Z
#define MAX_SOFTWARE_ENDSTOPS
  #define MAX_SOFTWARE_ENDSTOP_X
  #define MAX_SOFTWARE_ENDSTOP_Y
  #define MAX_SOFTWARE_ENDSTOP_Z
#define HOMING_FEEDRATE_XY (50*60)
#define HOMING_FEEDRATE_Z  (4*60)
#define VALIDATE_HOMING_ENDSTOPS
#define EEPROM_SETTINGS     // Persistent storage with M500 and M501
#define EEPROM_CHITCHAT       // Give feedback on EEPROM commands. Disable to save PROGMEM.
#define EEPROM_BOOT_SILENT    // Keep M503 quiet and only give errors during first load
  #define EEPROM_AUTO_INIT  // Init EEPROM automatically on any errors.
#define HOST_KEEPALIVE_FEATURE        // Disable this if your host doesn't like keepalive messages
#define DEFAULT_KEEPALIVE_INTERVAL 2  // Number of seconds between "busy" messages. Set with M113.
#define BUSY_WHILE_HEATING            // Some hosts require "busy" messages even during heating
#define PREHEAT_1_LABEL       "PLA"
#define PREHEAT_1_TEMP_HOTEND 185
#define PREHEAT_1_TEMP_BED     45
#define PREHEAT_1_FAN_SPEED     255 // Value from 0 to 255
#define PREHEAT_2_LABEL       "ABS"
#define PREHEAT_2_TEMP_HOTEND 240
#define PREHEAT_2_TEMP_BED    0
#define PREHEAT_2_FAN_SPEED     255 // Value from 0 to 255
#define PRINTJOB_TIMER_AUTOSTART
#define LCD_LANGUAGE en
#define DISPLAY_CHARSET_HD44780 JAPANESE
#define LCD_INFO_SCREEN_STYLE 0
#define SDSUPPORT
#define INDIVIDUAL_AXIS_HOMING_MENU
#define SPEAKER
#define REPRAP_DISCOUNT_FULL_GRAPHIC_SMART_CONTROLLER
#define SOFT_PWM_SCALE 0
#define SERVO_DELAY { 300 }

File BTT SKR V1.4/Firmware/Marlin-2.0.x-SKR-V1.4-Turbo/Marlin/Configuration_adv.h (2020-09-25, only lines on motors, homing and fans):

#define E0_AUTO_FAN_PIN -1
#define E1_AUTO_FAN_PIN -1
#define E2_AUTO_FAN_PIN -1
#define E3_AUTO_FAN_PIN -1
#define E4_AUTO_FAN_PIN -1
#define E5_AUTO_FAN_PIN -1
#define E6_AUTO_FAN_PIN -1
#define E7_AUTO_FAN_PIN -1
#define CHAMBER_AUTO_FAN_PIN -1
#define HOMING_BUMP_MM      { 5, 5, 2 }       // (mm) Backoff from endstops after first bump
#define HOMING_BUMP_DIVISOR { 2, 2, 4 }       // Re-Bump Speed Divisor (Divides the Homing Feedrate)
#define MICROSTEP_MODES { 16, 16, 16, 16, 16, 16 } // [1,2,4,8,16]

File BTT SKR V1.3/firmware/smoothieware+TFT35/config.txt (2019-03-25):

# Smoothieboard configuration file, see http://smoothieware.org/configuring-smoothie

# NOTE Lines must not exceed 132 characters, and '#' characters mean what follows is ignored

## Robot module configurations : general handling of movement G-codes and slicing into moves



# Delta configuration

# See http://smoothieware.org/delta

arm_solution                                 cartesian     # 笛卡尔    



extruder.hotend.enable                          true          # 使能挤出机，如果为false，相关的配置都将被忽略

# Arm solution configuration : Cartesian robot. Translates mm positions into stepper positions

# See http://smoothieware.org/stepper-motors

alpha_steps_per_mm                           80              # X轴运动1mm需要的步进数

beta_steps_per_mm                            80              # Y轴

gamma_steps_per_mm                           400             # Z轴

extruder.hotend.steps_per_mm                 100              # E轴运动1mm需要的步进数



# Cartesian axis speed limits

x_axis_max_speed                             12000            # X轴最大移动速率 mm/min

y_axis_max_speed                             12000            # Y轴

z_axis_max_speed                             150              # Z轴


alpha_max_rate                               12000.0          # X轴最大速率 mm/min

beta_max_rate                                12000.0          # Maxmimum rate in mm/min

gamma_max_rate                               150.0            # Maximum rate in mm/min


# Basic motion configuration

default_feed_rate                            2400             # G1/G2/G3的默认速率(mm/minute)

default_seek_rate                            2400             # G0的默认速率 (mm/minute)

mm_per_arc_segment                           0.5              # 圆弧分段的固定长度, 0 to disable

mm_max_arc_error                             0.01             # The maximum error for line segments that divide arcs 0 to disable








# Planner module configuration : Look-ahead and acceleration configuration

# See http://smoothieware.org/motion-control

acceleration                                 3000             # 加速度 mm/s^2

#z_acceleration                              500              # Z轴加速度 mm/s^2, 0 uses acceleration which is the default. DO NOT SET ON A DELTA

junction_deviation                           0.05             # See http://smoothieware.org/motion-control#junction-deviation

#z_junction_deviation                        0.0              # For Z only moves, -1 uses junction_deviation, zero disables junction_deviation on z moves DO NOT SET ON A DELTA





# Stepper module configuration 

# Pins are defined as  ports, and pin numbers, appending "!" to the number will invert a pin

# See http://smoothieware.org/pin-configuration and http://smoothieware.org/pinout

alpha_step_pin                               2.2              # X轴的step signal管脚

beta_step_pin                                0.19              # Pin for beta stepper step signal

gamma_step_pin                               0.22              # Pin for gamma stepper step signal

extruder.hotend.step_pin                     2.13              # 挤出的step signal管脚


alpha_dir_pin                                2.6              # X轴的方向stepper direction管脚, add '!' to 翻转电机运转方向

beta_dir_pin                                 0.20             # Pin for beta stepper direction, add '!' to reverse direction

gamma_dir_pin                                2.11!             # Pin for gamma stepper direction, add '!' to reverse direction

extruder.hotend.dir_pin                      0.11    	      # 挤出的方向dir signal管脚 ( add '!' to 翻转电机运转方向)


alpha_en_pin                                 2.1              # X轴使能管脚

beta_en_pin                                  2.8             # Pin for beta enable

gamma_en_pin                                 0.21             # Pin for gamma enable

extruder.hotend.en_pin                       2.12             # 挤出的使能信号


alpha_current                                0.9              # X轴驱动电流

beta_current                                 0.9              # Y stepper motor current

gamma_current                                0.9              # Z stepper motor current

delta_current                                0.9              # 挤出机1的驱动电流



## Extruder module configuration

# See http://smoothieware.org/extruder

extruder.hotend.default_feed_rate               600           # 挤出的默认速率 ( mm/minute )

extruder.hotend.acceleration                    10000         # 挤出的加速度mm/s^2

extruder.hotend.max_speed                       80            # 最大挤出速度 mm/s



# Extruder offset

#extruder.hotend.x_offset                        0            # X offset from origin in mm

#extruder.hotend.y_offset                        0            # Y offset from origin in mm

#extruder.hotend.z_offset                        0            # Z offset from origin in mm



# Firmware retract settings when using G10/G11, these are the defaults if not defined, must be defined for each extruder if not using the defaults

#extruder.hotend.retract_length                  3            # Retract length in mm

#extruder.hotend.retract_feedrate                45           # Retract feedrate in mm/sec

#extruder.hotend.retract_recover_length          0            # Additional length for recover

#extruder.hotend.retract_recover_feedrate        8            # Recover feedrate in mm/sec (should be less than retract feedrate)

#extruder.hotend.retract_zlift_length            0            # Z-lift on retract in mm, 0 disables

#extruder.hotend.retract_zlift_feedrate          6000         # Z-lift feedrate in mm/min (Note mm/min NOT mm/sec)




laser_module_enable                           false           # false失能激光模式



## Temperature control configuration

# See http://smoothieware.org/temperaturecontrol



# First hotend configuration

temperature_control.hotend.enable            true             # 使能hotend

temperature_control.hotend.thermistor_pin    0.24             # 热敏电阻连接的管脚

temperature_control.hotend.heater_pin        2.7              # 加热棒连接的管脚, 如果不需要设置为 nc 

temperature_control.hotend.thermistor        EPCOS100K        # See http://smoothieware.org/temperaturecontrol#toc5

#temperature_control.hotend.beta             4066             # Or set the beta value

temperature_control.hotend.set_m_code        104              # 设置温度的M-code

temperature_control.hotend.set_and_wait_m_code 109            # 设置并且等待温度达到目标的M-code

temperature_control.hotend.designator        T                # 这个模块的名称

#temperature_control.hotend.max_temp         300              # 最大温度，默认为300

#temperature_control.hotend.min_temp         0                # 最小温度



# Safety control is enabled by default and can be overidden here, the values show the defaults

# See http://smoothieware.org/temperaturecontrol#runaway

temperature_control.hotend.runaway_heating_timeout      0  # How long it can take to heat up, max is 2040 seconds.

temperature_control.hotend.runaway_cooling_timeout      0  # How long it can take to cool down if temp is set lower, max is 2040 seconds

temperature_control.hotend.runaway_range                0   # How far from the set temperature it can wander, max setting is 63掳C



# PID configuration 

# See http://smoothieware.org/temperaturecontrol#pid

temperature_control.hotend.p_factor         22.2             # P ( proportional ) factor

temperature_control.hotend.i_factor         1.08            # I ( integral ) factor

temperature_control.hotend.d_factor         114               # D ( derivative ) factor



#temperature_control.hotend.max_pwm          64               # Max pwm, 64 is a good value if driving a 12v resistor with 24v.





temperature_control.bed.enable               true             # 使能热床

temperature_control.bed.thermistor_pin       0.23             # 热敏电阻连接的管脚

temperature_control.bed.heater_pin           2.5              # 加热热床的管脚

temperature_control.bed.thermistor           EPCOS100K	      # See http://smoothieware.org/temperaturecontrol#thermistor

temperature_control.bed.set_m_code           140              # 设置热床目标温度的M-code

temperature_control.bed.set_and_wait_m_code  190              # 设置并等待热床达到目标温度的M-code

temperature_control.bed.designator           B                # 热床的名称

temperature_control.bed.runaway_heating_timeout      0  # How long it can take to heat up, max is 2040 seconds.

temperature_control.bed.runaway_cooling_timeout      0  # How long it can take to cool down if temp is set lower, max is 2040 seconds

temperature_control.bed.runaway_range                0   # How far from the set temperature it can wander, max setting is 63掳C





## Switch modules

# See http://smoothieware.org/switch



# Switch module for fan control

switch.fan.enable                            true             # 使能风扇

switch.fan.input_on_command                  M106             # 开风扇的M-code

switch.fan.input_off_command                 M107             # 关风扇的M-code

switch.fan.output_pin                        2.3              # 连接风扇的管脚
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

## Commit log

2019-03-01 initnial commit
    [Configuration.h, Configuration_adv.h]
2019-03-28 update tmc2130 spi homing sensorless
2019-03-29 add Schematic diagram
2019-06-20 BigtreeTech SKR 1.3 Case model
    BigtreeTech SKR 1.3 Case model
    [Anet A6 - SKR 1.3 motherboard case - 20 x 20 mounting.stl, Anet A6 - SKR 1.3 motherboard case.stl, Anet A6 - SKR 1.3 motherboard cover - 20 x 20 mounting.stl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]
2019-08-27 update firmware to lastest marlin version
    [Configuration.h, Configuration_adv.h, SKR-V1.3-BOM.xls]
2019-11-22 update lastest Marlin-bugfix-2
    [Configuration.h, Configuration_adv.h]
2019-11-23 SKR V1.3 pinout overlay picture
    I had trouble translating the pin diagram visually in my head. I don't imagine I'm the only one who feels like this, so I made this and wanted to share it
2019-11-23 Overlay text of pin diagram
    Overlay test of pin diagram for easier decoding visually
2019-12-13 add SKR V1.4 manual
    [Anet A6 - SKR 1.3 motherboard case - 20 x 20 mounting.stl, Anet A6 - SKR 1.3 motherboard case.stl, Anet A6 - SKR 1.3 motherboard cover - 20 x 20 mounting.stl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]
2019-12-17 update skr v1.4 pin
    [Configuration.h, Configuration_adv.h]
2019-12-31 SKR_V1.4_Turbo (#183)
    [Configuration.h, Configuration_adv.h]

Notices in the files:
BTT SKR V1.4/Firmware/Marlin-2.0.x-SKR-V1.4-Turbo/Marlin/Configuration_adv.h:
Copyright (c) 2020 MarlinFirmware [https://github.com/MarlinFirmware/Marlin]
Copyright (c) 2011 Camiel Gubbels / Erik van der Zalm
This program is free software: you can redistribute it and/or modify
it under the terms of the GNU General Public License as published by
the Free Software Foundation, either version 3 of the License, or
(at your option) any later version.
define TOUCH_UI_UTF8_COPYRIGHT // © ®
